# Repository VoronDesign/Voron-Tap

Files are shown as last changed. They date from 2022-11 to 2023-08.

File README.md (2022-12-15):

# Voron Tap

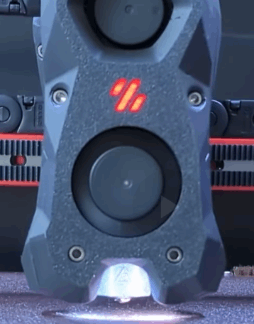
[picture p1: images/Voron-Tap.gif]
Voron-Tap3


> Animated image courtesy of [Maple Leaf Makers](https://github.com/MapleLeafMakers) , see the whole video at https://www.youtube.com/watch?v=mz5qcOZgXhI

Tap is a nozzle-based z-probe for the V2 and Trident printer designs. The entire toolhead moves to trigger an optical switch. Tap offers many advantages:

* Extreme precision 0.4μm (0.0004mm)
* Any build surface and easily change at will
* Durability via optical sensor (millions of probe cycles)
* High temperature reliability (70C to 100C)
* Simplified probe mechanics (no dock/undock macros)
* No separate Z-endstop required
* Crash protection

## Requirements

* Bed must be stable for probing force of 500-800 grams
  * Switchwire, V1.8, Legacy, V0 beds are NOT rigid enough
* Mounts to MGN-12H X-axis
* Front mounted extruder (Clockwork2, LGX, Galileo)
* Accuracy depends on good mechanical condition
* Must have 5V at toolhead or special 24V sensor PCB

## Instructions

Comprehensive assembly details are available in the [Manual](Manual/Assembly_Manual_Tap.pdf)

## Post-Install Setup

1. Update your `printer.cfg` as recommended in [Tap Klipper Instructions](config/tap_klipper_instructions.md)
2. Home Z and test virtual Z endstop by lifting tool-head
3. Heat soak your machine and run a couple `probe_accuracy samples=100` to "break-in" your probe
4. Run a few more `probe_accuracy` checks (default of 10 probes)

For well-built machines you can expect to see between 0.0000 and 0.0008 standard deviation.

## FAQs

* Will Tap hurt my print surface? No, probing temp is restricted to 150C. The team recommends spray coated spring steel. Users of smooth PEI may find minor burnish marks if continously probing the same spot.
* Will the hartk 2-piece PCB work with Tap? Yes, but it requires a slight modification. See discord pin.
* Can I use an optical sensor not specified in the BOM? Not recommended, the team spent considerable time validating sensors in [BOM](BOM.md).
* Can I use micro-switch instead? Not recommended, but check here for more details: [Unklicky Tap](https://github.com/majarspeed/Unklicky/tree/main/Unklicky_TAP)
* Can I use Tap with kinematic bed mounts? Yes, if your bed is rigid up to 800 grams of force.
* Doesn't this add a lot of weight? The team explored many designs and landed on ~50 extra grams as good trade-off between rigidity and weight.
* Why do I need this if my induction probe works fine? Tap enables a far better user experience as it eliminates most baby-stepping needed due to thermal expansion, nozzle & bed surface changes.
* Is Tap noticably more accurate than klicky? Yes.

## (Bonus Points) Data Science

Tap engineering is backed by data science. If you want to dive deeper check out the following resources:

* [Voron:LIVE! Voron Tap announcement stream](https://www.youtube.com/watch?v=JLUDLJQXZeU)
* [Probe accuracy across thermal envelope](https://github.com/KiloQubit/probe_accuracy)
* [Repeatability at individual corners](https://github.com/sporkus/probe_accuracy_tests)

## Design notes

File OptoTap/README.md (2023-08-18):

# OptoTap PCB

OptoTap PCB is a small, completely unnecessary PCB that exists to make installation of the optical sensor marginally more convenient. (That's right, several of us have spent dozens of hours and hundreds of dollars in order to avoid two solder joints and a bit of heat shrink.)

It comes in two official flavors/form factors:

- **V1**: smaller form factor, 5V only
- **V2**: taller form factor, 5 or 24V capable

Both simplify optical sensor installation by including the necessary current-limiting resistor for the IR led within the sensor itself, as well as providing a visible LED indicator to assist with troubleshooting. 

The V1 board attempts to minimize size and cost as much as possible, at the expense of some flexibility: it **can not be used as a drop-in replacement for 24V inductive sensors** (24V will fry the optical sensor, eventually.)

The V2 board adds a switch-mode regulator to allow safely connecting to 24V probe headers. The regulator converts positive input voltage between >5V and 24V to 5V on-board, at the expense of some additional components and a larger PCB. **Please read important information about previous versions of this board below.**

## OptoTap V1

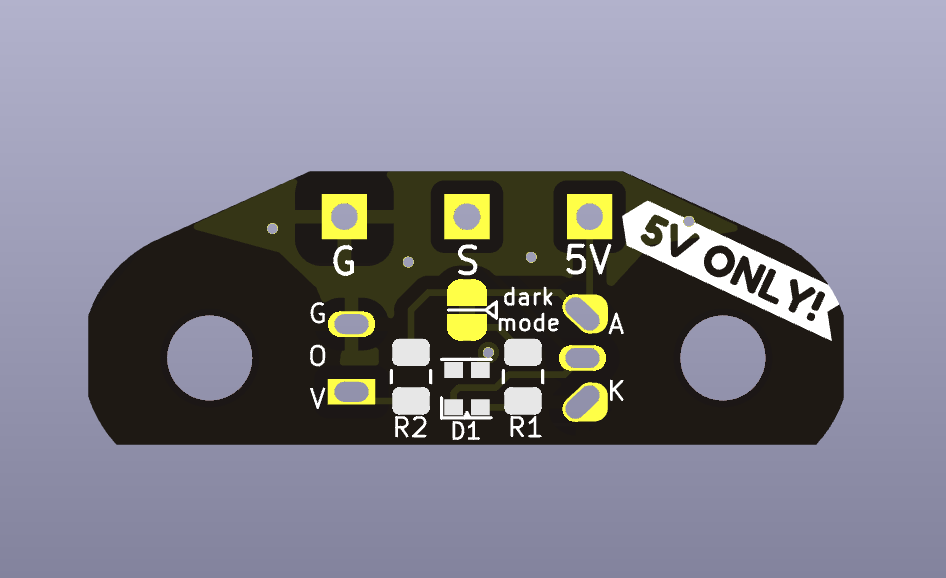
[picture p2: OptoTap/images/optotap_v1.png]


This version saves some vertical room by requiring you to solder your connector wires directly to the board.

**Do not connect this version to 24V!** (Did we mention that *it's not 24V tolerant???*) Many of the Voron toolhead PCBs in circulation send 24V to the three-pin probe header. You cannot plug this board directly in to these headers!

### Revision history 

- 1.0: initial release
- 1.3: updated release
	- hybrid footprint to permit use of EE-SX398 sensor in addition to Optek versions
	- two-color LED to indicate status and assist with troubleshooting.
	- 'Dark Mode' solder jumper to allow turning off indicator LEDs
	- increased thermal relief on solder pads to make through-holes easier to solder

## OptoTap V2

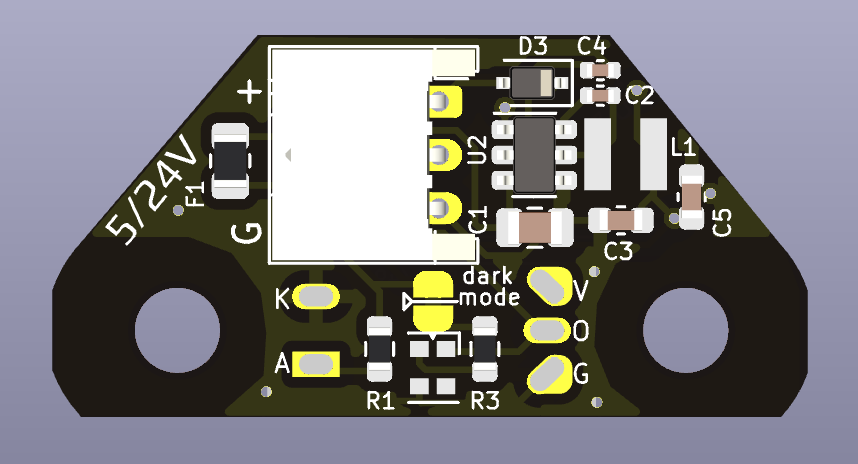
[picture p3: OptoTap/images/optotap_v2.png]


This version uses an AP63205WU switch mode regulator to drop input voltage and supply 5V to the sensor. This gives a bit of additional room to add a 3-pin JST-PH 2.0mm pitch connector as well [part number S3B-PH-K-S (LF)(SN)].

**IMPORTANT NOTE: The original version of this board had an issue that rendered it unsafe for use at 24V**. Please see [this issue](https://github.com/VoronDesign/Voron-Tap/issues/42#issuecomment-1370065351) for more extensive details on the testing and resolution of the problem. 

The current version (V2.4) fixes the inrush overvoltage spike that plagued the initial release, and adds several additional safeguards, including a polyfuse and a reverse polarity protection diode.

### Usage notes

#### Operation at 5V

The V2.4 OptoTap PCB has been tested to work fine from 5V to 24V inputs with no modifications. However, this does induce a bit of additional voltage drop from the switching regulator IC going into LDO mode. If you would like to run the V2.4 OptoTap at 5V, my first suggestion would be to just run it at 5V with no modifications. It will most likely work just fine. 

However, it does have the capacity to bypass the whole buck converter circuit. Note that this also bypasses the polyfuse, so there will be no overcurrent protection. 

To make this modification, you need to cut the trace between the center pad and 24V pad on the rear of the PCB, then use some solder to bridge the center pad to the 5V pad. To reverse the change, just desolder that bridge and re-connect the center pad to the 24V pad with more solder. 

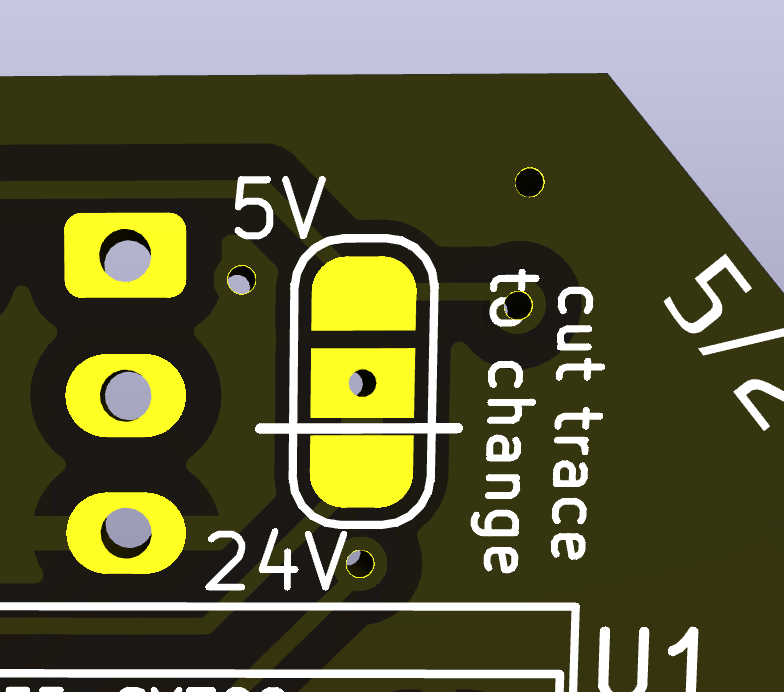
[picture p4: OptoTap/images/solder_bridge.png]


### Revision history

- 2.0: initial prototype
- 2.1: component modifications after initial testing
  - changed C1 to higher voltage rating
  - changed C2 bootstrap cap to higher capacitance
  - changed all capacitors to 0805 for better part availability
- 2.4: updated release
  - added polyfuse to limit overcurrent and damp inrush current-induced voltage spike on hot-plugging
  - added reverse polarity protection diode 
  - increased size of inductor to prevent coil saturation
  - added a second output filter capacitor to reduce output voltage ripple
  - hybrid footprint to permit use of EE-SX398 sensor in addition to Optek versions
  - two-color LED to indicate status and assist with troubleshooting.
  - 'Dark Mode' solder jumper to allow turning off indicator LEDs
  - added 5V/24V selection solder jumper on rear of board to allow for easy bypassing of voltage regulator circuit
  - increased thermal relief on solder pads to make through-holes easier to solder

### Ordering and Assembly notes

#### Inductor choice

I've tested version of this PCB with inductors from Cenker 
CKCS3012-4.7uH/M (C354557) and Microgate 
MPIT3015-4R7M-LF (C486485). Any 30xx footprint coil inductor with >1A current rating and ~ 100 mΩ DCR should work ok.

#### Indicator LED placement

For some reason, JLCPCB has trouble with their part orientation for this LED specifically. I'm hoping that eventually they will sort their database out. In the meantime, it is worth verifying the part placement prior to assembly.

The footprint silkscreen has two elements to help indicate the orientation of the LED: an extra line on the side to indicate Pin 1, and a little arrow that matches up with a corresponding arrow on the part:

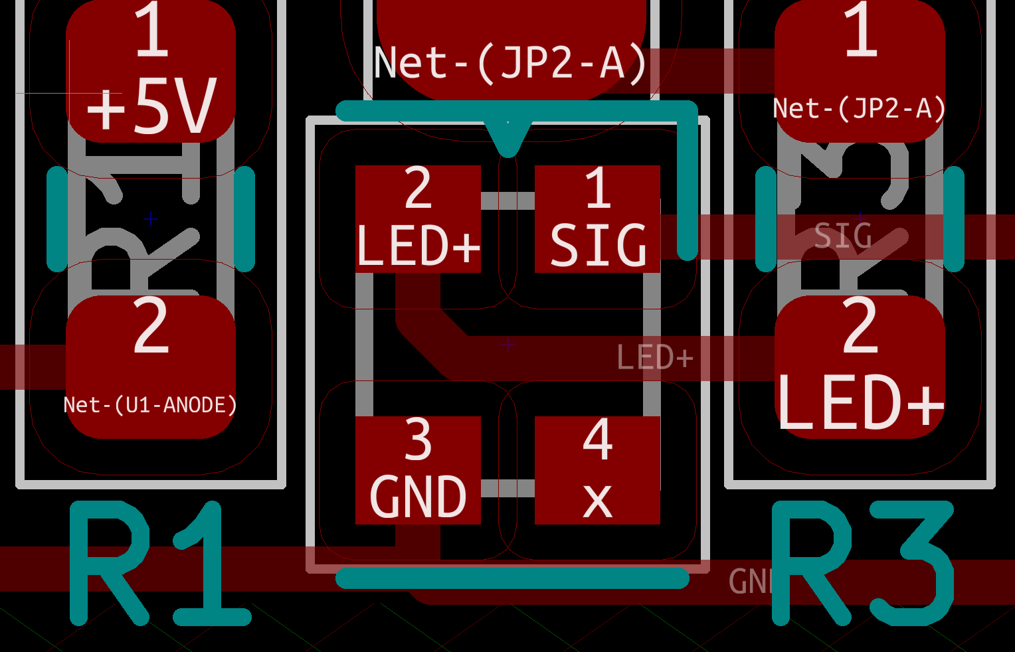
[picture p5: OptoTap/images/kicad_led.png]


For the v2.4 PCB, make sure that the arrow on the DFM points to the arrow on the footprint, pin 1 matches the extra line on the footprint, and the + pad matches up to the correct pad! 

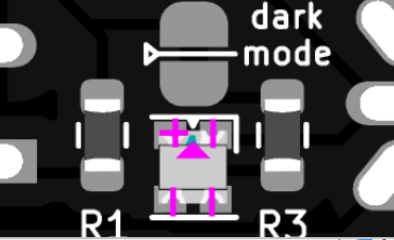
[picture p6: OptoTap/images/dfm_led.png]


This is how it will look when assembled:

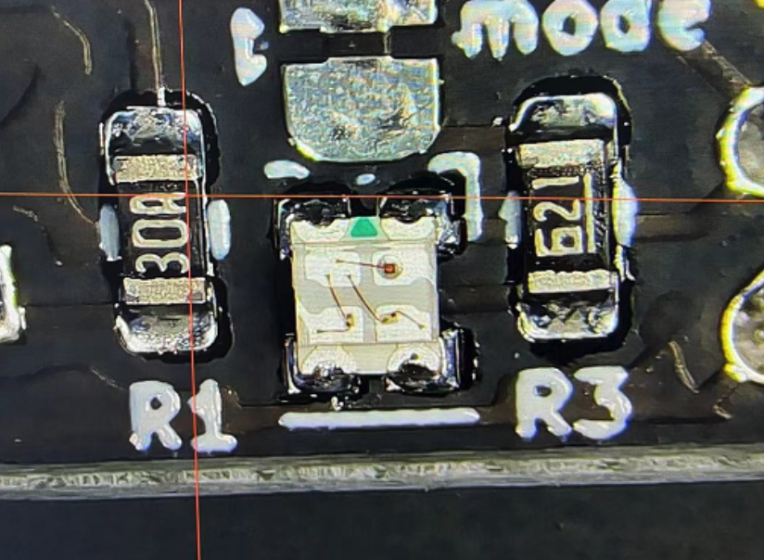
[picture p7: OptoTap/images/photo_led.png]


You can see the little bond wires from each of the three LEDs going back to the common anode, which is pretty neat.

***NOTE THAT THE 5V ONLY BOARD (V1.3) HAS A ROTATED FOOTPRINT! YOU'RE WELCOME AND I'M SORRY.***

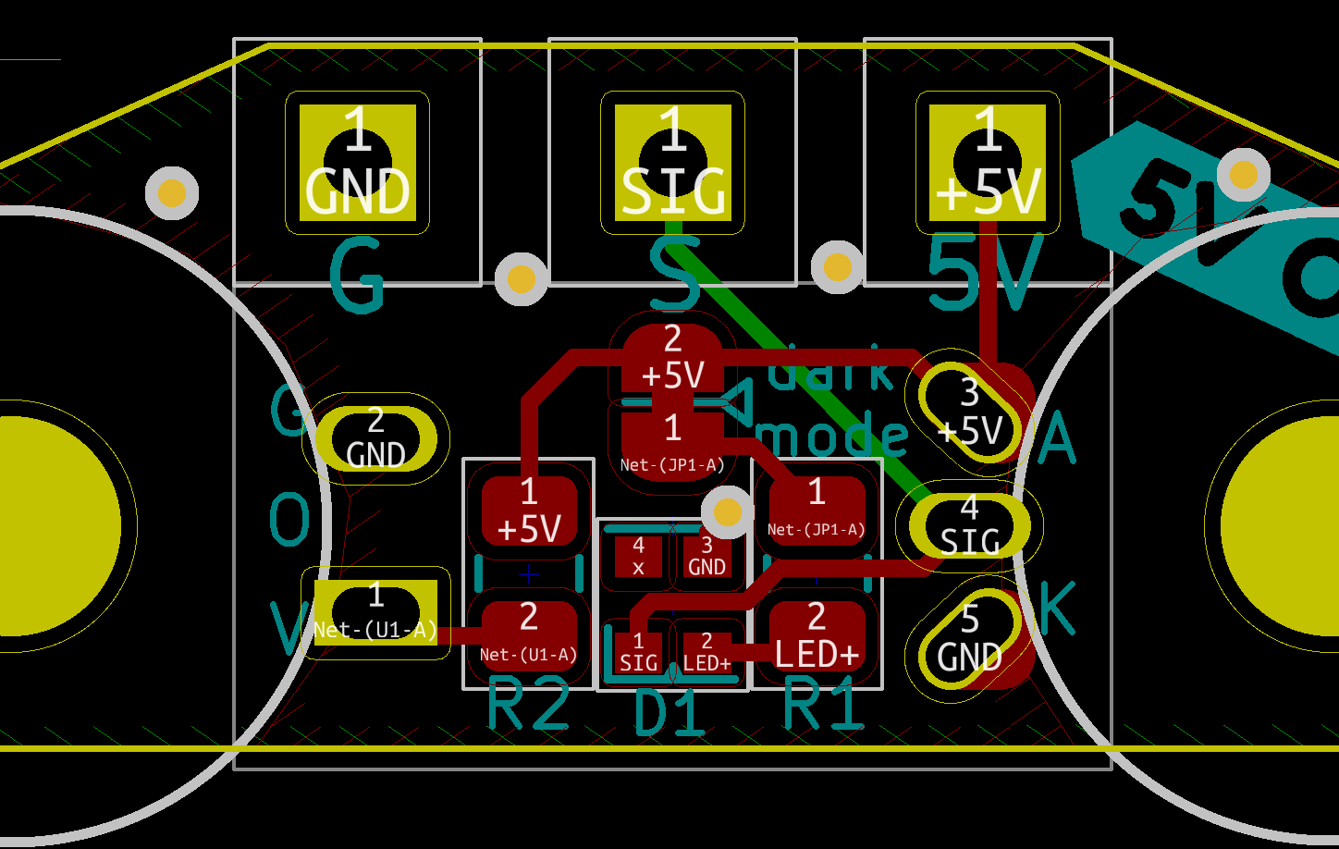
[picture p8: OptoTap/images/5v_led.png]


## Indicator LEDs

The revised boards (V1.3/2.4) now have two-color indicator LEDs to help assist with troubleshooting. This should hopefully help a little bit with troubleshooting. The expected behavior of the LED is:

- Blue: Connected to power, beam not broken
- Red: Connected to power, beam broken

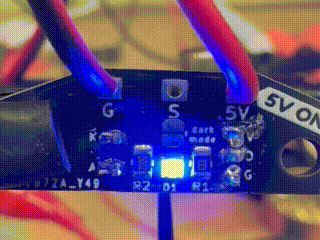
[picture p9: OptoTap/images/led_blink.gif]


When installed in the toolhead, the light should be red normally (toolhead in 'down' position) and blue when activated (toolhead in 'up') position.

I would suggest powering on the board with 5V prior to installing it to make sure everything is functioning as expected. If the indicator LED is red with nothing blocking the optical sensor beam path, there is probably a problem with the ground and signal wires -- triple check!

## Sensor Choice

### Omron or Optek

The revised versions of the boards (V1.3 and V2.4) feature a hybrid optical sensor footprint that permits installation of the Omron EE-SX398 sensor in addition to the Optek OPB666/9xx versions. In testing, the Omron sensor performed just as well as the Optek sensor. 

However, it has a *slightly* different footprint than the Omron sensor, with annoyingly-close leads on the three pin side. I went through a few iterations of testing to come up with a hybrid footprint that seems to work well for either sensor model.

The slots mean there is a little play in sensor positioning, particularly with the EE-SX398 sensor. To help ensure precise alignment with this sensor, print out the jig included in the [STLs](./STLs) folder.

### Sensor Logic

The Tap setup requires a *buffer* style circuit rather than an *inverter* style to ensure safe operation. This style causes the sensor to trigger (pull the signal pin low) when the toolhead is in its normal, 'down' position. That means that if there is a bad connection somewhere, the MCU can observe that there is a problem *without* crashing the toolhead uncontrollably into the build plate.

Please double check your sensor part number to make sure you're getting the appropriate model!

#### For Omron:

- **Good**:
  - EE-SX398
- **Bad**: 
  - EE-SX498

#### For Optek:

- **Good**: 
  - OPB666N
  - OPB9x1
- **Bad**:
  - OPB9x2

Additionally, for the Optek probes, the OPB9x0 sensors are totem pole rather than open collector, meaning that they will pull the sense pin up to 5V when not pulling it down to GND. This can cause problems for some boards (notably RP2040-based CAN toolhead boards) that do not have 5V-tolerant endstop pins.

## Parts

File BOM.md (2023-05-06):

# Bill of Materials

|Category|Qty|Description|Notes|
|:----|:----|:----|:----|
|Hardware|1|50 mm MGN9 Rail|see cutting guide, Ends deburred, overall length +/- 1 mm|
|Hardware|1|MGN-9H Carriage|Medium preload (Z1) is preferred, but regular preload will work. Carriage must be removable from rail.|
|Hardware|2|6 mm x 3 mm magnet|6 mm diameter, 3 mm tall cylinders.  N52 strength preferred,  N35 or higher strength required.|
|Hardware|11|M3 Heatset Insert|Standard Voron spec 4.7 mm diameter inserts|
|Hardware|3|H3 Hex Nut|ISO 4032|
|Hardware|8|M3 Washer|DIN 125, 7mm outer diameter, 0.5 mm thickness|
|Hardware|2|M3 x 20 SHCS|Socket head cap screw|
|Hardware|3|M3 x 16 SHCS|Socket head cap screw|
|Hardware|3|M3 x 12 SHCS|Socket head cap screw|
|Hardware|1|M3 x 6 SHCS|Socket head cap screw|
|Hardware|2|M3 x 6 FHCS|Flat head cap screw. MUST BE MAGNETIC.  No stainless, may be black oxide or zinc coated.|
|Hardware|2|M3 x 12 BHCS|Button Head Cap Screw|
|Hardware|2|M3 x 8 BHCS|Button Head Cap Screw|
|Hardware|10|M3 x 6 BHCS|Button Head Cap Screw|
|Hardware|2|M3 x 50 BHCS/SHCS|Button or Socket Head Cap Screw, fully threaded|

Optionally you can replace the M3 x 6 FHCS with additional magnets. See [R8_errata.md](Manual/R8_errata.md) for details

## Sensor Options:  Select either “Wired Sensor” or “PCB Sensor"

**Wired**
|Category|Qty|Description|Notes|Links|
|:----|:----|:----|:----|:----|
|Electronics|1|220 Ohm resistor | ¼ Watt, +/- 10% tolerance resistor| |
|Electronics|1|OPB Wired Sensor|Optek sensor, wired. OPB991| |
| | | |OPB991P51Z| |
| | | |OPB991L51Z| |
| | | |OPB991T51Z| |
| | | |OPB991T11Z|https://www.digikey.com/short/rrjtmvwm|
| | | |OPB991L11Z|https://www.digikey.com/short/cnnhjr5n|

**PCB Sensor**
|Category|Qty|Description|Notes|Links|
|:----|:----|:----|:----|:----|
|Electronics|1|OptoTap v2 PCB| | |
|Electronics|1|OPB PCB Sensor|Optek sensor: OPB666N or OPB971N51| |
| | | |OPB666N|https://www.digikey.com/short/f2mzw5rm|
| | | |OPB971N51|https://www.digikey.com/short/m9rz73fp|

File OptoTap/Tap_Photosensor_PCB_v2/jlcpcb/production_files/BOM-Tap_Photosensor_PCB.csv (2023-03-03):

Comment | Designator | Footprint | LCSC
D_Schottky | D3 | D_SOD-323 | C146335
AP63205WU | U2 | TSOT-26 | C2071056
620R | R3 | R_0603_1608Metric | C23220
Polyfuse_Small | F1 | R_0805_2012Metric | C2840557
100 nF | C2 | C_0402_1005Metric | C307331
4.7 uH | L1 | CKCS3010 | C354557
68 nF | C4 | C_0402_1005Metric | C354977
10 µF | C1 | C_0805_2012Metric | C440198
200R | R1 | R_0603_1608Metric | C8218
22 µF | C3,C5 | C_0603_1608Metric | C84419
XL-1615RGBC | D1 | LED_0606_1432 | C965840

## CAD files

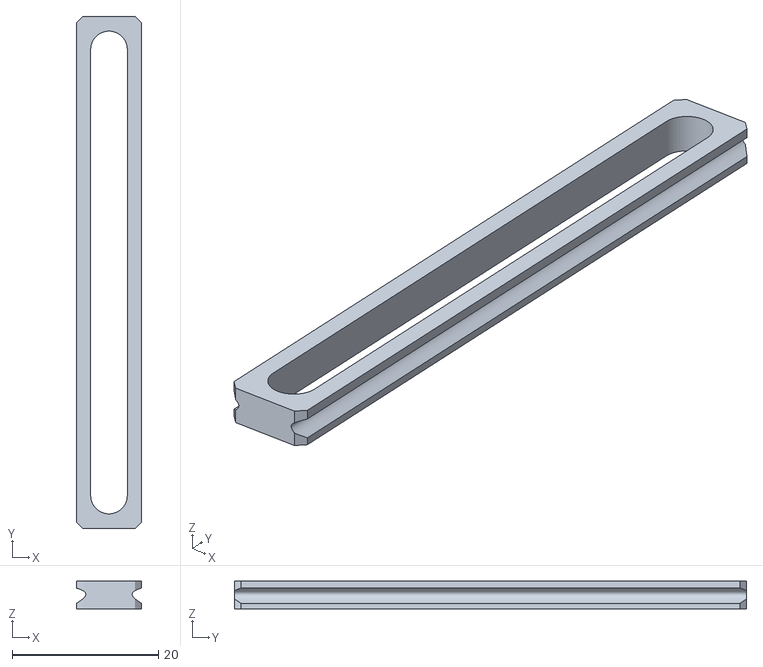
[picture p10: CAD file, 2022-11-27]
STLs/MGN9_Assembly_Tool.stl
8.90 x 70.0 x 3.80

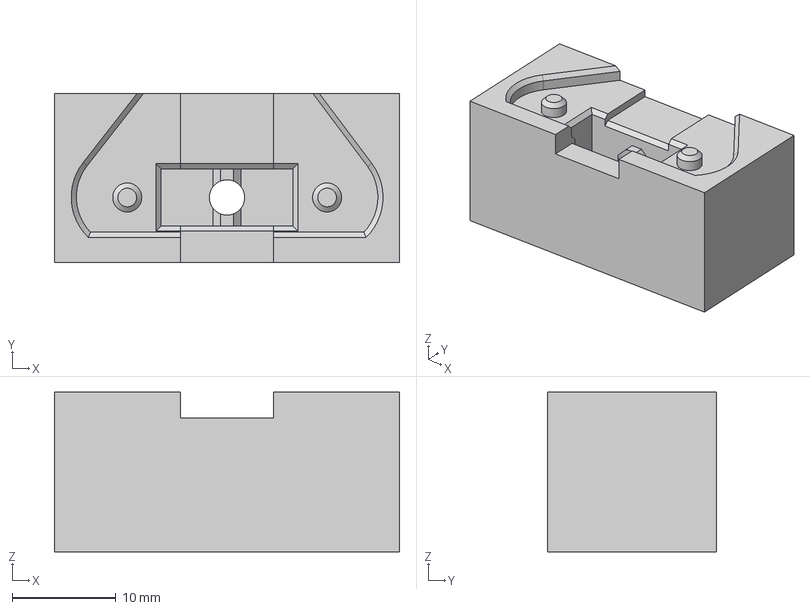
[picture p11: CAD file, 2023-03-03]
OptoTap/STLs/solder_jig.step
33.2 x 16.2 x 15.4 mm

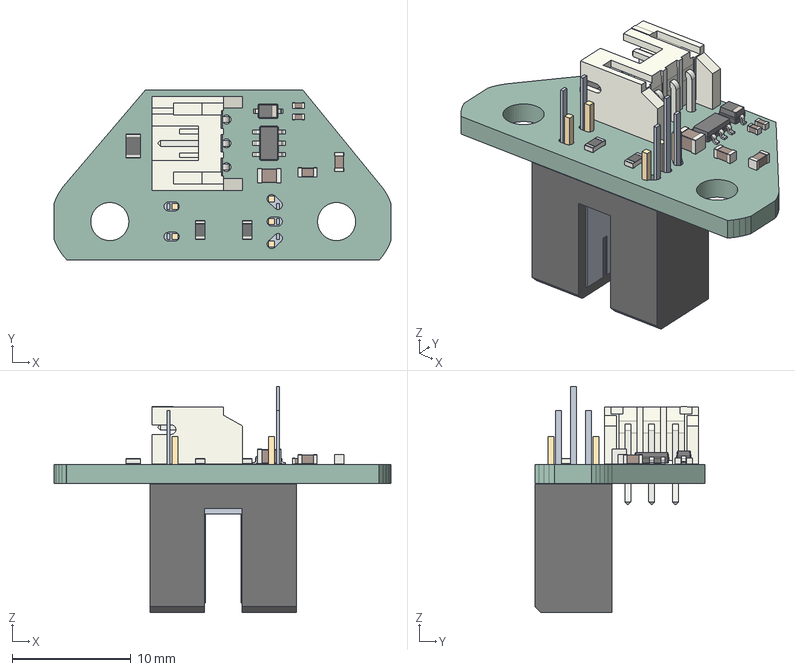
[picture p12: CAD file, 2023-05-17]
OptoTap/Tap_Photosensor_PCB_v2/Tap_Photosensor_PCB.STEP
28.3 x 14.3 x 19.0 mm
PCB

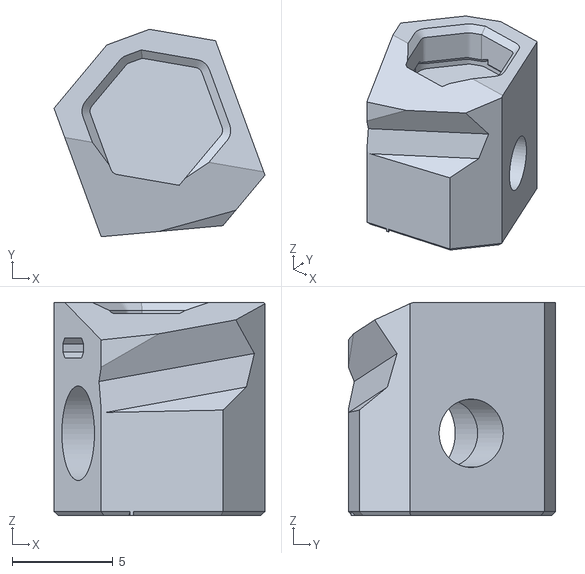
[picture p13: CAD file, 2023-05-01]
STLs/Tap_Center_right_r8.stl
10.5 x 10.3 x 10.6

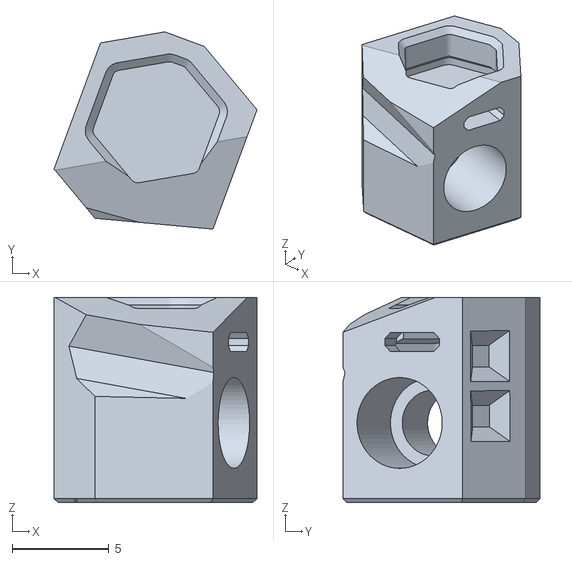
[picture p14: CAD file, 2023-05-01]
STLs/Tap_Center_left_r8.stl
10.5 x 10.2 x 10.6

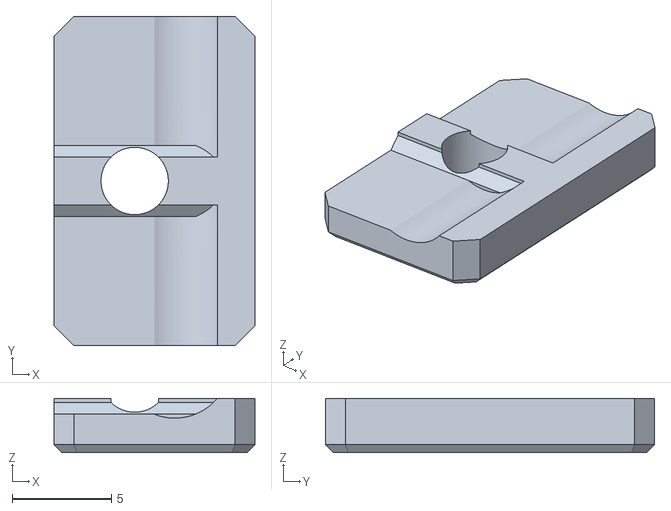
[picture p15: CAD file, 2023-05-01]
STLs/[a]_Tap_Belt_Cover_r8_x2.stl
10.1 x 16.6 x 2.74

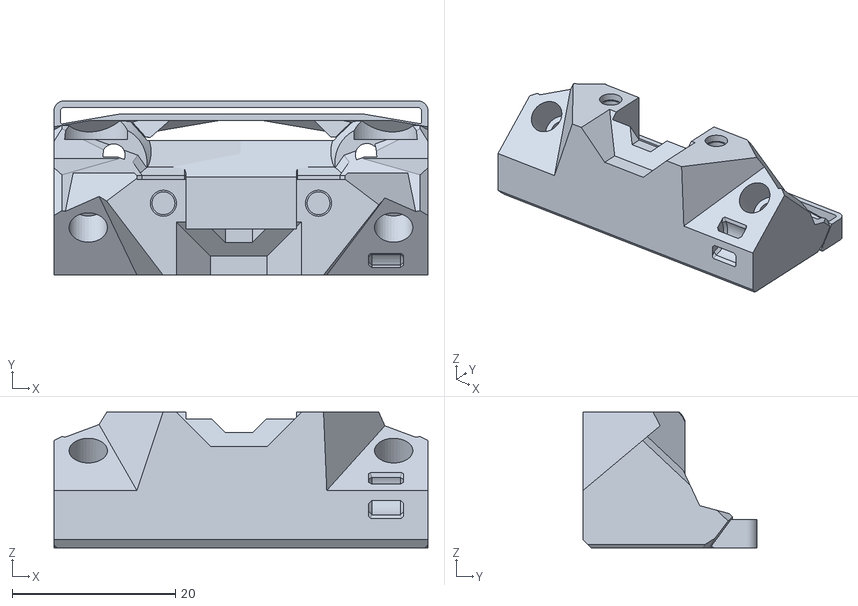
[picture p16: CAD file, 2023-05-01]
STLs/Tap_Upper_PCB_r8.stl
45.8 x 21.3 x 16.6

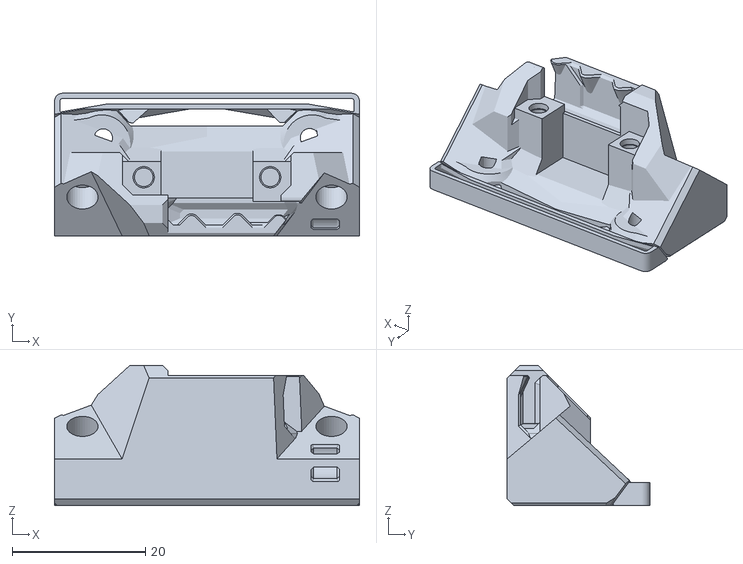
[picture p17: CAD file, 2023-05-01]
STLs/Tap_Upper_Wired_r8.stl
45.8 x 21.4 x 21.1

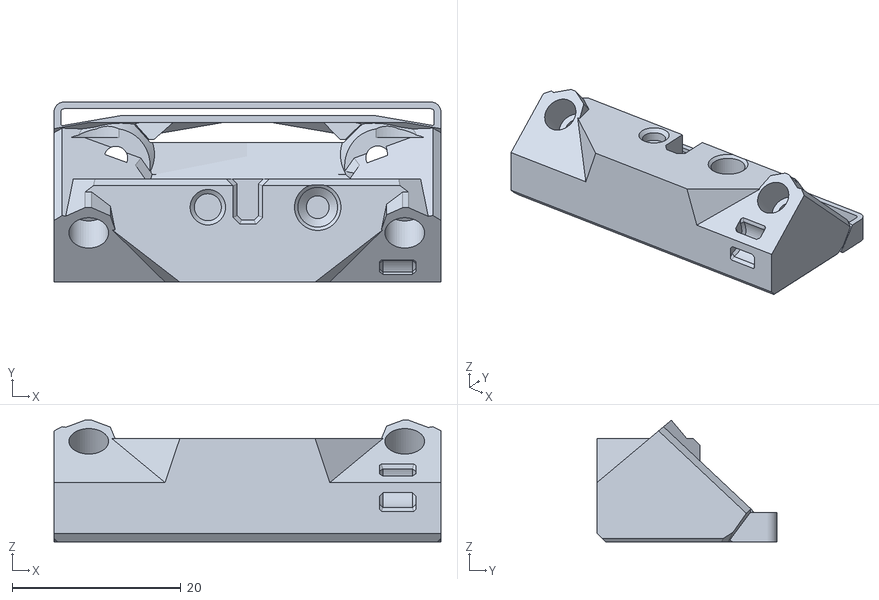
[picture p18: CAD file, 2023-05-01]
STLs/Tap_Upper_D2HW_r8.stl
45.8 x 21.3 x 14.4

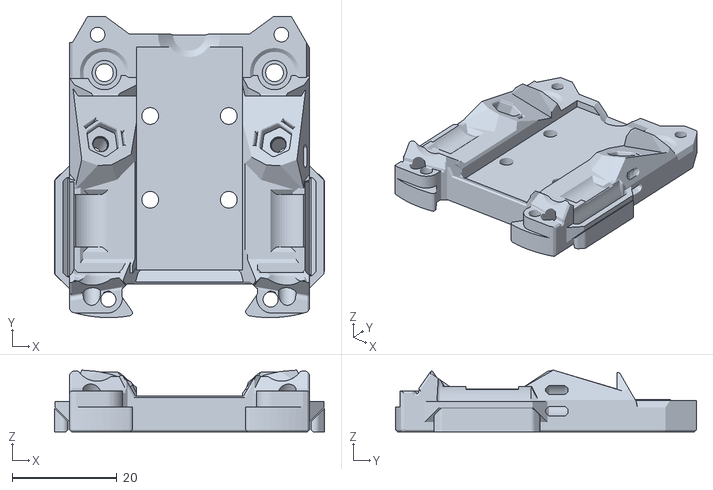
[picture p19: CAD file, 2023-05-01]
STLs/Tap_Front_r8.stl
51.6 x 57.5 x 11.8

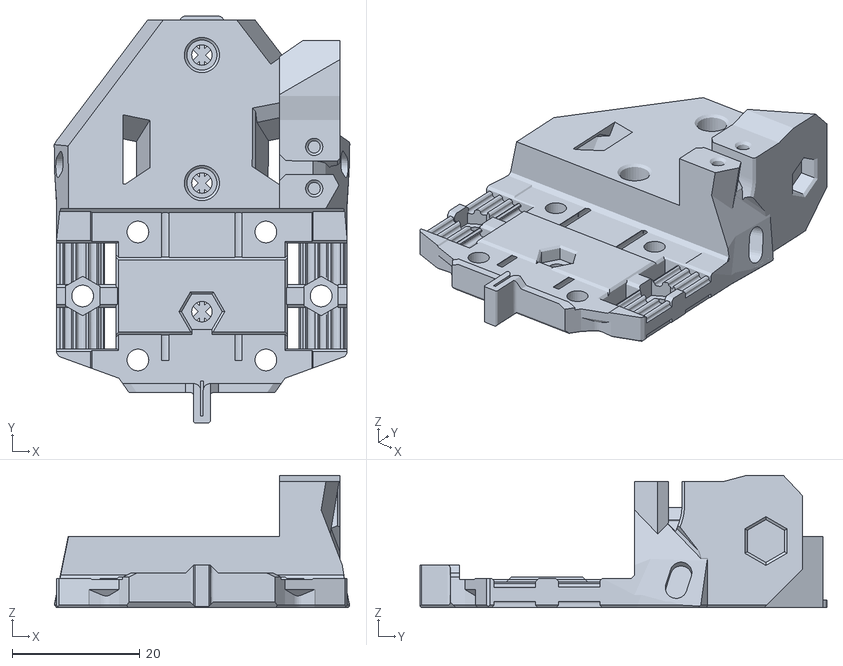
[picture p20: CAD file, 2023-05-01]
STLs/[a]_Tap_Center_r8.stl
46.2 x 63.6 x 20.7

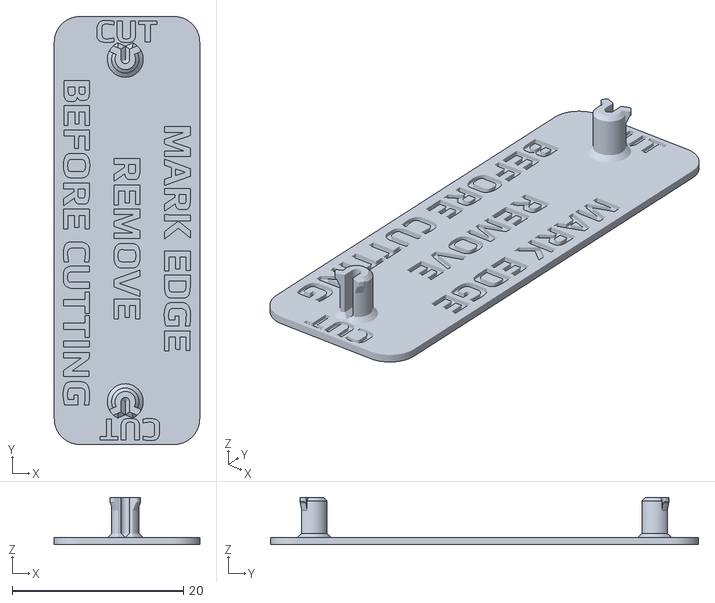
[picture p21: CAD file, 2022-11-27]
STLs/Printed_Cut_Guide.stl
17.0 x 50.0 x 5.50

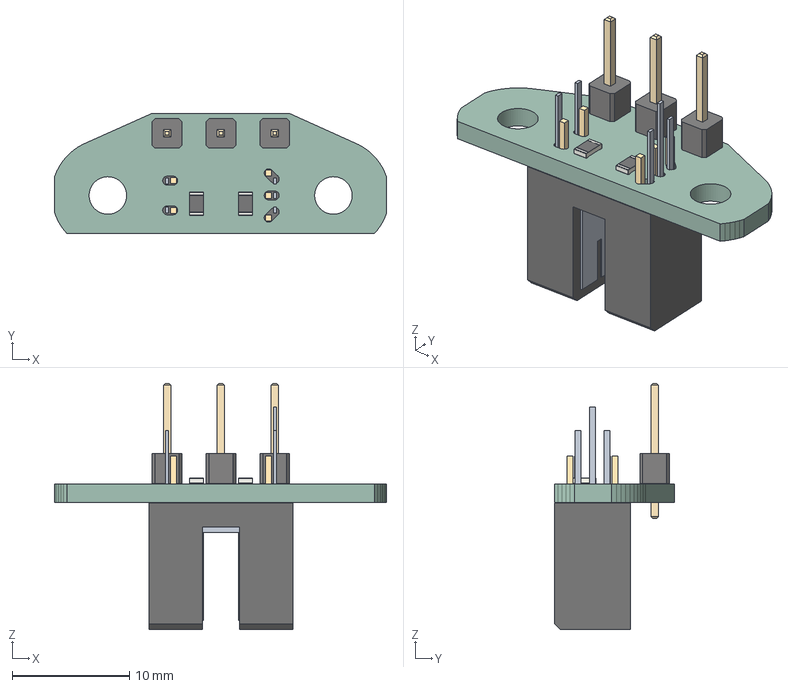
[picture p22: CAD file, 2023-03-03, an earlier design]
OptoTap/Tap_Photosensor_PCB_v1/Tap_Photosensor_PCB_Short_ee-sx.STEP
28.3 x 10.2 x 21.0 mm
PCB

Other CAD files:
OptoTap/STLs/optotap_eeSX398_solder_jig.stl
OptoTap/Tap_Photosensor_PCB_v2/Tap_Photosensor_PCB_v2.4.STEP

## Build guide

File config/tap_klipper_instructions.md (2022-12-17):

# Updating your Klipper config for Tap

There are a few changes you'll need to make in order to get Tap working properly.

1. Update your Z endstop: 
   
   - Under the `[stepper_z]` block, you'll want to comment out your `position_endstop` and change your `endstop_pin` so that it uses the virtual Z endstop for Tap.
   
      - Example: `endstop_pin: probe:z_virtual_endstop`
   
   - Be sure to *also* remove any automatically saved `[stepper_z] position_endstop: ...` value that may be found at the **bottom** of your `printer.cfg`file.

2. Update your Z homing position: 
   
   - If you use `[safe_z_home]`, change the location to the center of the bed. If you have a `[homing_override]` make sure that it moves the toolhead to the center of the bed before calling `G28 Z`.
   
3. Update your probe's offsets: 
   
   - Remember, with Tap, your nozzle IS the probe, so your `[probe] x_offset` and `[probe] y_offset` values should be 0 now. You'll need to manually calibrate the probe's Z offset by using `PROBE_CALIBRATE`.
   
4. Add Tap's `activate_gcode:`  
   
   - This G-code will allow you to probe cold, but will also prevent you from probing with a nozzle at printing temperature (to try to preserve your build surface). This goes in the `[probe]` section of your config.  

```jinja

activate_gcode:
    {% set PROBE_TEMP = 150 %}
    {% set MAX_TEMP = PROBE_TEMP + 5 %}
    {% set ACTUAL_TEMP = printer.extruder.temperature %}
    {% set TARGET_TEMP = printer.extruder.target %}

    {% if TARGET_TEMP > PROBE_TEMP %}
        { action_respond_info('Extruder temperature target of %.1fC is too high, lowering to %.1fC' % (TARGET_TEMP, PROBE_TEMP)) }
        M109 S{ PROBE_TEMP }
    {% else %}
        # Temperature target is already low enough, but nozzle may still be too hot.
        {% if ACTUAL_TEMP > MAX_TEMP %}
            { action_respond_info('Extruder temperature %.1fC is still too high, waiting until below %.1fC' % (ACTUAL_TEMP, MAX_TEMP)) }
            TEMPERATURE_WAIT SENSOR=extruder MAXIMUM={ MAX_TEMP }
        {% endif %}
    {% endif %}
    
```

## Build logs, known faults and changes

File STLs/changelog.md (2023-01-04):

The scope of this file is to summarize any stl changes after the initial release files (r1)
Important note:  When a change is made it is normal for only a few parts to change, or a single part to change.  For parts that don't change, we do not increment revision numbers.
As a result of this, the revision numbers of the most current parts may not match.

11/28/2022
[a]Tap_Center_r2: fixed a minor issue in the MGN12H chamfer that would cause some MGN12H carriages to not fit properly (issue 15)
https://github.com/VoronDesign/Voron-Tap/issues/15

11/29/2022
[a]Tap_Center_r3: re-added in the support structure that went missing at [a]Tap_Center_r2

12/16/2022
[a]Tap_Center_r4: reinforced area above magnet holders
Tap_upper_D2HW_r1: new variant for switch
Tap_upper_PCB_r2: minor changes to optical sensor location for better trigger
Tap_upper_wired_r2: repositioned sensor to same location as PCB
Tap_front_r2: increased clearance to M3x12 endstop

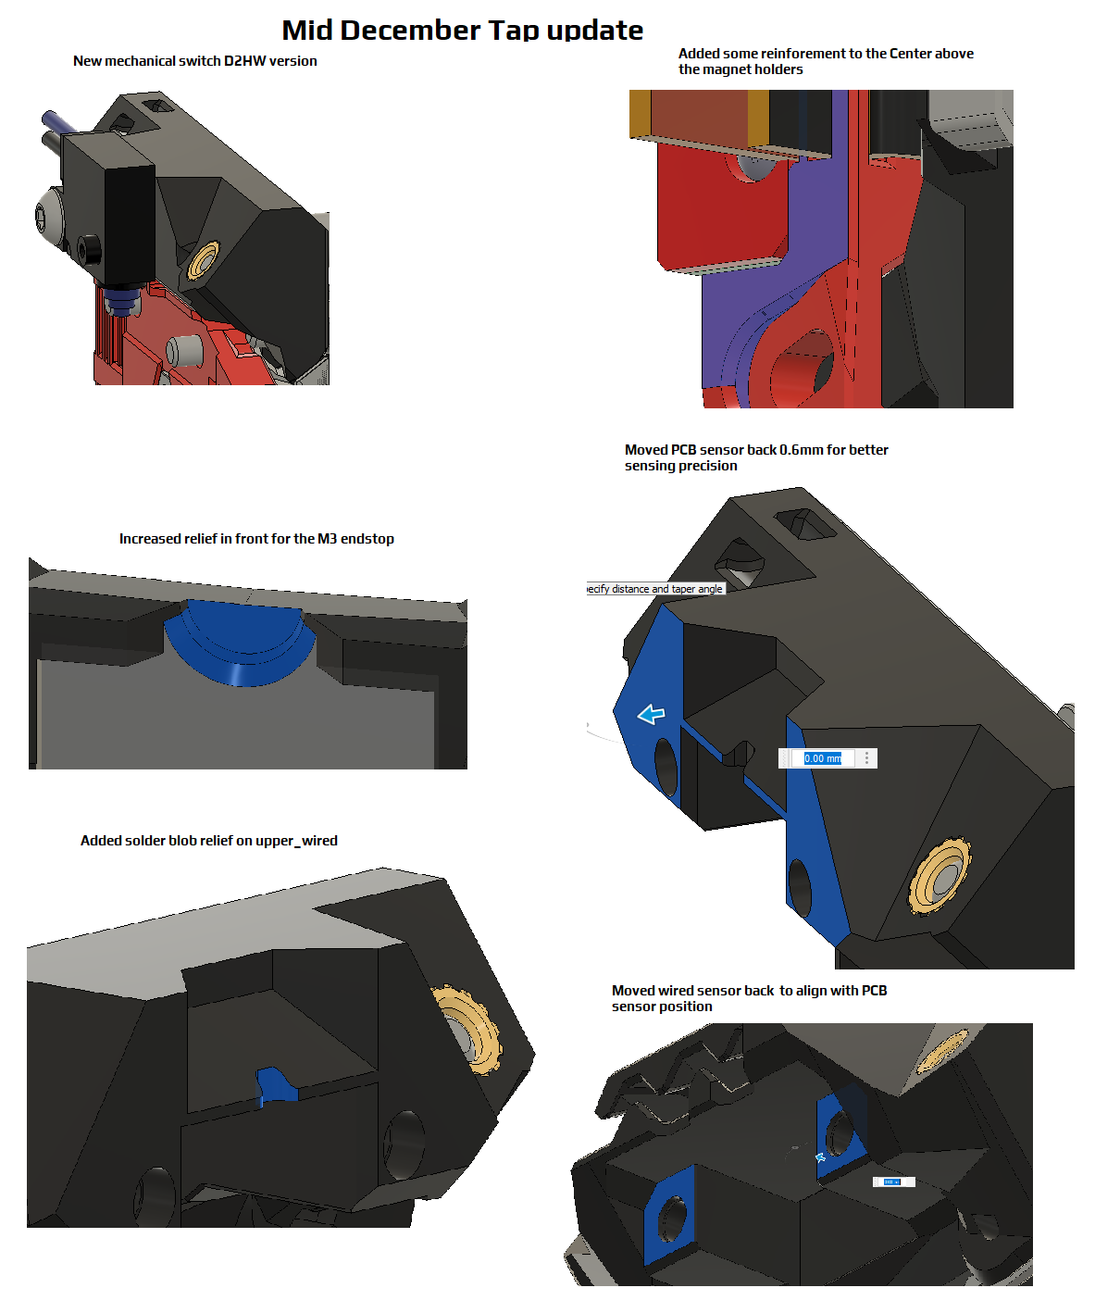
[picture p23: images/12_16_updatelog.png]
Mid December Update


1/3/2023
[a]Tap_Center_r5: eliminates binding issues caused by belts pressing on endcaps, also better belt management
moved X-switch 1mm to right to activate before collision
[a]Tap_Center_r6: removed a small artifact that began in r5
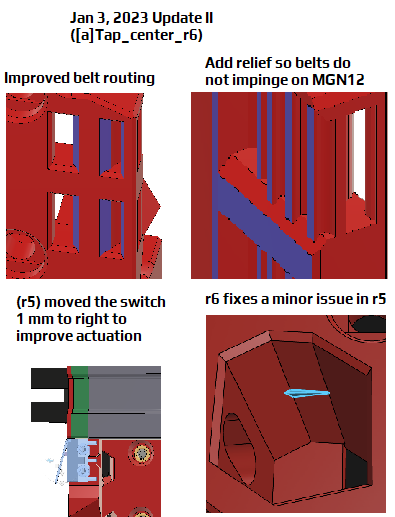
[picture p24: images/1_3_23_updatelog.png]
Jan 3 Update


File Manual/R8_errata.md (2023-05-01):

TAP RC8 Errata, notes, etc

Welcome to Tap RC8.  This is a full reprint from Tap RC6.

*Wait! What happened to RC7? the last thing you published was RC6!*  
RC7....didn't make it.  From its ashes, RC8 arose.  As we all know, eight is great.  
  
Here's what changed:

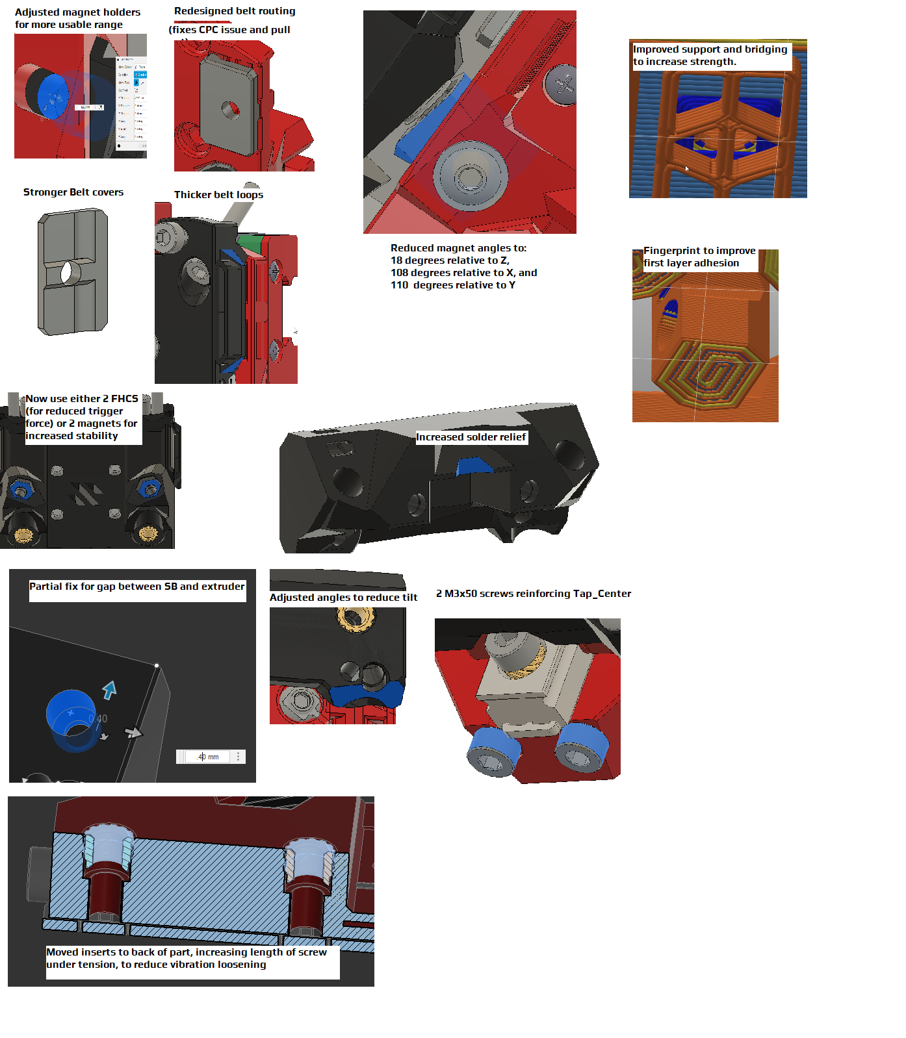
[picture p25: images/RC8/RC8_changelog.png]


One of the big changes is you can now use either a pair of magnets or a pair of FHCS in Tap_front.  The stronger the pull force, the more resistant to ringing, but also the more potential to marring your Build surface.  
  
here are my reccommendations.  this is a guideline only, your mileage may vary, caveat emptor, barba crescit caput nescit.

| Build surface | Trigger force (approx) | Configuration | Max Accels |
|---|---|---|---|
| Flat PEI sticker | 750 g | 2 N35 magnets + 2 FHCS | 5000 mm/s^2 |
| Powder coat PEI | 1400g | 4 N52 Magnets | 10000 mm/s^2 |

Other than possibly wanting more or stronger magnets, here's what you will need in addition to the original Tap BOM:

| Qty | Description | Notes |
|-----|---|---|
| 2 | M3x50 BHCS or SHCS | Threaded the entire length. you can get by without these, or with M3x40's.  |
| 1 | M3x16 SHCS | Replaces a M3x12 SHCS securing the rail. |
| 2 | M3x8 BHCS | Used with belt covers |
| 2 | M3 nuts | Used with belt covers |
| 2  | M3 washers | Used with belt covers |
| 11-12 | M3 Heatset inserts | This depends on your ability to reclaim heatsets from the existing parts.  If you can, you won't need any additional heatsets. |

Belt handling:  
The belts are now handled by looping around Tap_center, and secured with a printed belt cover and M3x8 BHCS:

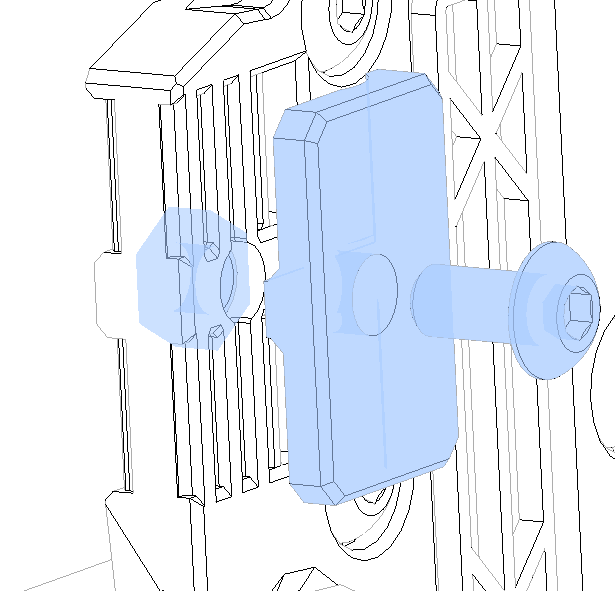
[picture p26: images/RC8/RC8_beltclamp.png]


the 2 M3x50 bolts are threaded up into Tap_Center, and serve to provide extra stiffening:

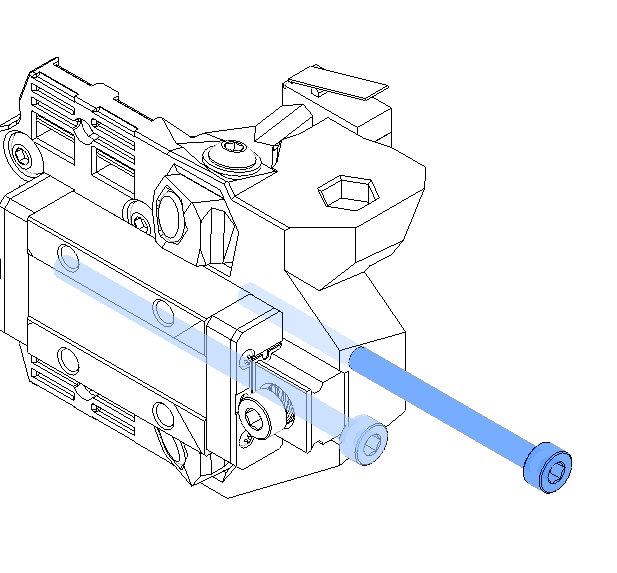
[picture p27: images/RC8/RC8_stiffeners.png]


The heatset inserts for the center are moved back 4 mm to provide extra vibration resistance:

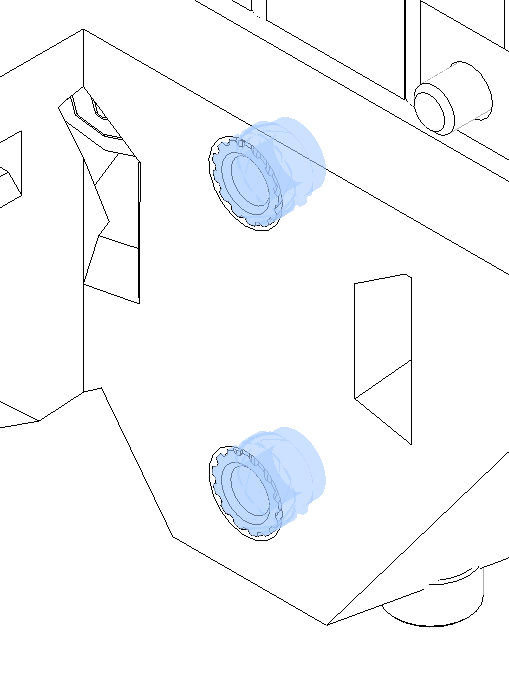
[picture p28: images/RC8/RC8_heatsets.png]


So they will need to be secured with M3x12 and M3x16 SHCS:

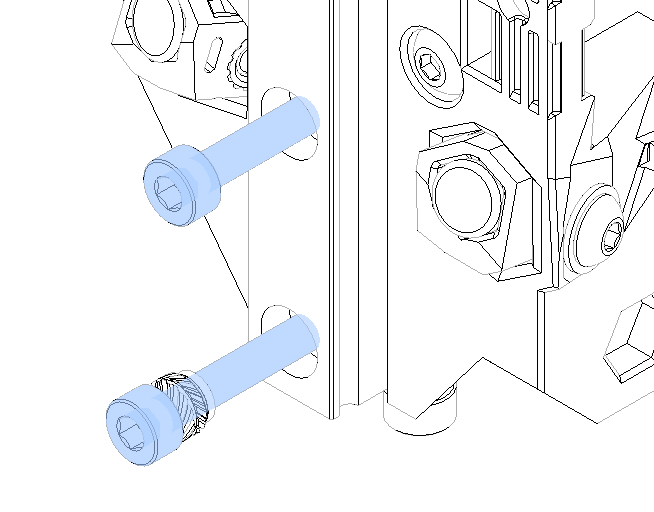
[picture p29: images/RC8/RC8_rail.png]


(The top is still secured by M3x6 SHCS)

Enjoy!

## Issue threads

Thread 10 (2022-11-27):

Fun Fact Voids™

Durahl, 2022-11-27:
The on Page 27 of the Manual mentioned `Fun Fact Voids™` didn't appear with my settings of **SuperSlicer** and since I couldn't figure out what settings was responsible for them not to make an appearance I went ahead and enlarged them to a 0.2mm gap which then sliced them as intended.

Maybe consider increasing them in the STLs like I did or give a mention in the Manual what Slicer setting may be responsible for them to appear ( or not )?

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

pl4nkt0n, 2022-11-28:
You can see them within the STEP:
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

I think, your slicer is closing this gaps because of too high "gap closing radius". There should be the same function with different names in different slicers.

notgwj, 2022-11-28:
The SuperSlicer setting that causes this is actually `hole_size_compensation` (`XY compensation`).  Setting it to zero makes the voids work as intended.  See https://discord.com/channels/460117602945990666/1041007230239125574/1046753665270165574

Badnoob-327, 2022-12-13:
"This part has thin voids inside it (blue).  When the part is sliced, these produce internal ribs which strengthen the part.  If your slicer closes these up, recheck your slicer settings for hole size compensation. Default voron slicer profiles are available for voron printers."

Hows that? I wanted to keep it general as there are other settings that could affect this.

notgwj, 2022-12-13:
Looks good to me.

nemgrea, 2022-12-27:
fixed via https://github.com/VoronDesign/Voron-Tap/pull/32

Closed 2022-12-27.

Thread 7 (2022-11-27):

(small) Error in the Assembly Manual

laserbeak, 2022-11-27:
Hi,
Just wanted to point out a small error in the assembly manual. An unfinished sentence(or did I miss the punchline?).
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

laserbeak, 2022-11-27:
OOH! And another.
Looks like there's some truncation happening?
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

Badnoob-327, 2022-11-27:
and some pictures got pixelated out as well.

nemgrea, 2022-11-28:
will be fixed via https://github.com/VoronDesign/Voron-Tap/pull/16

Closed 2022-11-28.

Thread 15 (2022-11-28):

MGN12 Carriage does not lay flat on Tap_Center

joseph-greiner, 2022-11-28:
I was looking at the CAD for the Tap an noticed interference between the MGN12 carriage and the tap_center component. I printed the STL in the repo, mounted the carriage with the belts installed and noticed that the parts mount at a slight angle to each other.

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

The issue is that the chamfer for the bottom of the carriage on the tap_center part is too big and will not let the carriage lay flat, even with belts installed.

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

By cutting out the large chamfer and adding a 0.4mm chamfer to the area the carriage now lays flat.

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

Modified STL and STEP files can be provided if requested.

Badnoob-327, 2022-11-28:
it appears that some MGN12's have a different chamfor spec than others, I will update the STL.

Badnoob-327, 2022-11-29:
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

please look at the updated tap_center_r2 file and let me know if you see need for more than that, I like to keep some chamfer there if possible

joseph-greiner, 2022-11-29:
I am printing it now, I will update when it is finished, but the support was not exported with the part STL.

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

joseph-greiner, 2022-11-29:
Printed the r2 STL, the carriage sits flat now.

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

Badnoob-327, 2022-12-06:
I think this can be closed now, thank you for your feedback.

Closed 2022-12-06.

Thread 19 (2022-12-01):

Wrong link to "Tap-Klipper Instructions"

GuidoHendriks, 2022-12-01:
First things first; I'm so impressed with this project! Thanks a lot. 👍🏻

---

Now the minor issue with the manual...

On page 37 of the manual it says:

> The software setup and other initial setup steps with your new printer can also be found on our documentation page. We recommend starting with the **Tap-Klipper Instructions** on our Github.

This contains a wrong link.

Have double checked that I have the latest file. Also noticed this https://github.com/VoronDesign/Voron-Tap/issues/14 which also does not seem to be fixed in the latest file. Maybe it's not committed or pushed to Github yet?

Badnoob-327, 2022-12-13:
got it , and I rerefixed the #14, appreciate the reminder.

nemgrea, 2022-12-27:
fixed via https://github.com/VoronDesign/Voron-Tap/pull/32

Closed 2022-12-27.

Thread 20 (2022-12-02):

Assemble Sensor instructions should address position of solder work

ditdafivo, 2022-12-02:
I assembled my OBP991T11Z to basically look identical to the picture on the manual page 13, even to the same scale, but as a result there isn't enough space to route the wires with the shrink tube, soldering joints etc. in the wiring channel of Tap_Upper_Wired_r1.stl.

I'm thinking now the best place for all the solder work is so that it lives along side all the rest of the concealed wiring for the tool head.  In fact for the second try, I might not even do that solder work until the sensor body is screwed into Tap_Upper_Wired and the wires are installed in the wiring channel. I'm not sure if that's what others are doing or if specific length guidelines can make sense to document in the manual given the variety of toolheads, canbus mods etc.  But at least it would be helpful to note on that manual page that the picture is not meant to show the extra length required between the sensor body and the resistor/solder work/shrink tube to route through the wiring channel.

ditdafivo, 2022-12-05:
Having now fitted my stealthburner/CW2, I'd leave at least 30mm wire untouched out of the sensor body to be able to conceal with work safely under the toolhead wiring cover.

kyleisah, 2022-12-13:
@ditdafivo hey there, I made the graphic you're referring to. It wasn't really *intended* to be used to scale, but I can see how that would happen, and I think I would feel better having the actual components being tucked inside the cable door with everything else. I've got the CAD I made, wired sensors, and gumption. Maybe I just overlooked that with all the excitement. 😅 I'll talk to the right people and see what we can do to improve that.

Badnoob-327, 2022-12-16:
the intent there is actually to have the resistor tucked into the wire channel, I'll clarify the manual

ditdafivo, 2022-12-17:
I don't see how fitting inside the wire channel could have worked for my build. Maybe I needed smaller resistors/heatshrink. Or maybe I overextruded.

nemgrea, 2022-12-27:
fixed via https://github.com/VoronDesign/Voron-Tap/pull/32

Closed 2022-12-27.

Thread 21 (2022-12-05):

Holes for CW2 mounting not centered.

krankydonkey, 2022-12-05:
Upon reviewing the CAD, it appears that the holes for the CW2 Mounting on Tap Upper Wired part are off centre, causing them to be out of alignment with the CW2 holes when it is inserted into the slot.
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

Badnoob-327, 2022-12-06:
Hi, thank you for the question.  I would not use the sides as reference, as their location is determined by other geometry

I rechecked the CAD, and relative to the hotend mounting screws there is a slight offset showing of approx .08 mm. This should not cause any real issues with assembly or operation, and has not caused any issues I'm aware of.

gji, 2022-12-10:
I also noticed some more centering issues on the center body - it looks like the MGN9 rail inset is a bit less than 0.1mm off as well, from the center of the holes. Seeing as people have this working it probably doesn't matter so much functionally, but it does make any modifications a pain since the CAD is pretty far from symmetric (e.g. the belt and magnet holes are also not symmetric) so one has to be very careful when picking reference surfaces.

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

Badnoob-327, 2022-12-16:
I'm aware of it, thank you.

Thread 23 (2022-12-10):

Typo in manual about BOM heatset inserts

contrapuntal, 2022-12-10:
In the BOM on pg15: "These are standard Voron inserts, 4.7 mm diameter and 4mm tall"

4.7mm refers to the hole size in CAD. Voron standard threaded inserts are 5mm diameter.

Badnoob-327, 2022-12-13:
you are absolutely correct. thank you!

nemgrea, 2022-12-27:
fixed via https://github.com/VoronDesign/Voron-Tap/pull/32

Closed 2022-12-27.

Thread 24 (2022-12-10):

Brass threaded insert causing magnet not to sit flush

contrapuntal, 2022-12-10:
A M3x5x4 threaded insert causes bulging in the magnet holder, so that the magnet won't sit flush.
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

mrmultifunk, 2022-12-11:
I had this happening as well. What worked for me, was to reheat the insert and press the bulging down with an Allen key.

krankydonkey, 2022-12-12:
What I found worked was inserting the magnet first and then putting the heat set insert in while holding the magnet flush with the side with a ruler

Badnoob-327, 2022-12-13:
I think krankydonkey has a good idea, and we can fix that in documentation (by switching the order and doing magnets before heatets.

Badnoob-327, 2022-12-16:
Next manual has the order of operations switched (magnets in first, then inserts), so this should be fine

ps-bond, 2022-12-20:
> Next manual has the order of operations switched (magnets in first, then inserts), so this should be fine

Is there an issue with breaking the adhesive if that's done?  My usual way of releasing superglued parts is to warm them...

Badnoob-327, 2022-12-20:
I've not had any issues with the superglue getting loose here, if you wish you could try RTV instead of superglue.

ps-bond, 2022-12-20:
Actually I've been using Loctite 480...  I've been using the stuff for a while to glue magnets to prints and have found it more resilient than standard CA.  Probably overkill, admittedly.

nemgrea, 2022-12-27:
fixed via https://github.com/VoronDesign/Voron-Tap/pull/32

Closed 2022-12-27.

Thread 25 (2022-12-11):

Manual errata P29 - "When tightened, the M3x12 head will still be above the rail surface and act as a carriage" - "stop" missing?

ps-bond, 2022-12-11:

Badnoob-327, 2022-12-16:
Thank you, I'll get itin the next rev.

nemgrea, 2022-12-27:
fixed via https://github.com/VoronDesign/Voron-Tap/pull/32

Closed 2022-12-27.

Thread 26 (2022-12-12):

klipper config instruction should instruct the user to remove position_endstop

MapleLeafMakers, 2022-12-12:
When using probe as a virtual endstop, the `position_endstop` setting for stepper_z needs to be removed / commented out.  this should be called out in the instructions.

KiloQubit, 2022-12-12:
It is already called out in the instructions
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

MapleLeafMakers, 2022-12-12:
Apologies, I don't know how I missed that

Closed 2022-12-12.

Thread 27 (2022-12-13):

More information for [stepper_z] section in klipper firmware manual for Tap needed.

kyleisah, 2022-12-13:
Hey there! Small issue, but I think it should also be mentioned that you'll need to remove the `[stepper_z] position_endstop` that *may also* be present at the **bottom** of printer.cfg from previous configuration.

Thanks! ❤️

Badnoob-327, 2022-12-16:
sounds good, feel free to do a pr on that

hyperphonic0, 2022-12-16:
Duplicate of #26 (and it is already mentioned in the instructions: https://github.com/VoronDesign/Voron-Tap/blob/main/config/tap_klipper_instructions.md).

kyleisah, 2022-12-17:
@hyperphonic0 I think you may have misread the issue. Yes, the current instructions tell you to comment out `[stepper_z] position_endstop` but it really should also mention to remove it from the bottom of your config, like what happens when klipper does a `save_config` command to save your new endstop value from before installing Tap. It's there at the bottom where it can be easily forgotten or missed.

Closed 2022-12-17.

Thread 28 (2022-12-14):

Opb961 + electric components fix for manual

artemen, 2022-12-14:
Not all listed opb sensors have color coded wires, for example opb961 has only pins.
Page 13 right hand side picture is really confusing - at first it looks just like the opb sensor view from the button, and if connecting based solely on the looks (very natural given how the rest of the manual is very visual) one can burn mcu.
If just assume that the view is from the bottom it's pretty harmless and just won't work, however if you compare it to the schematic and see that cathode and anode pins are switched in the picture one can assume that it's the view from the top, this will result in short circuiting of the 5v rail on the mcu.
The truth is that page13 picture is neither the top nor the bottom view, but rather a diagram with pins rearranged to make it look neater.
Either include a warning that the picture below is a diagram, or adjust it to make it look as the most useful view- from the bottom.

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

Badnoob-327, 2022-12-16:
Hi, thanks for your comment.  OPB 961 is not a recommended sensor for the Wired option, as it has only pins.  The only wired sensors I have recommended are OPB 991 P51Z , OPB 991 L51Z, OPB 991 T51Z, OPB 991 T11Z

Closed 2023-01-02.

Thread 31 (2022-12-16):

Documentation: X endstop should be shown in different orientation

top-gun, 2022-12-16:
Hi,

I use an X-endstop mounted to the toolhead. In my case it's a KW11, but I saw the same issue with an Omron D2F-L on Discord.

The documentation (page 30) shows the endstop with the latch opening to the bottom. Due to the shape of the XY-joiner, the endstop will not trigger in this orientation. With the endstop mounted in reverse position (latch opening to the top), it will hit the XY-joiner reliably.

I think the documentation should show the endstop with the latch opening to the top so people use the working position.

ditdafivo, 2022-12-17:
For me, even flipping it upside down didn't trigger. I ended up gluing a piece of plastic onto the XY Joint, through on discord someone suggested that bending the lever a little might have been enough.

hyperphonic0, 2022-12-25:
The current Trident CAD shows it in the described orientation.

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

W141-ID, 2022-12-27:
@ditdafivo had/have the same issue. As you suggested I bented the lever which ended up in breaking it's plastic guard, but it seems to work for now.
Just to be clear, lever is still on, just the lever guard has broken off. Now it can make a 45deg turn.

top-gun, 2023-01-12:
Fixed as of Center part R6.

Closed 2023-01-12.

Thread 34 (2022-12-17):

update FAQ regarding hartk pcb

Surion79, 2022-12-17:
In the FAQ, it is mentioned that the hartk PCB must be changed to be compatible, this is not true for the v2.x OptoTap PCB, which does support 24v. It should be mentioned before users with a v.2x OptoTap PCB is scratching their hartk toolhead pcb unnessecarily and producing possible errors/issues in their build

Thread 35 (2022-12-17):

Center void on magnet holders different sizes.

blgli, 2022-12-17:
The circle indentations that were added to Tap_Magnet_Left_r1 and Tap_Magnet_Right_r1, are different depths.

Not sure which is correct but on Tap_Magnet_Left_r1 it is 0.2mm deep and on Tap_Magnet_Right_r1 it is 0.1mm deep, also these STL's are not included in the latest CAD.

Badnoob-327, 2022-12-17:
Hi, thanks for pointing this out.  Those indentations were temporary features to help align the magnets for manual images.  They are not needed and are not in the current CAD, I'll update the STLs to remove them, but there should be no effect on performance.

Closed 2022-12-27.

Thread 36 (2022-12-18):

X-Rail mount step doesn't say it's mounting to X-Rail

mobilemcclintic, 2022-12-18:
On Page 29, the manual shows putting (4) M3x6 BHCS into the holes that mount to the X-Rail carriage.  Right after that, it notes about installing the X end stop magnet.  In my mind, I'd install the magnet when the assembly is off the machine, so I was dropping screws as I was glue and pressing the proximity magnet in.

Maybe it should have a picture of the X-Rail carriage in the image so it's explicitly shown that it is being physically connected to the machine.  Maybe it's just me.

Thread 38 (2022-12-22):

Chamfer in hole

Lelle79, 2022-12-22:
I have a chamfer in the angled holes for bolting "tap upper" to "tap front". is that supposed to be there? the slicer picture is upside down. sorry for that.

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

nemgrea, 2022-12-27:
that feature is to prevent the slicer from creating overhung bridges in that area. your image shows the part being sliced in the in correct direction. in real life the parts bolt up just fine, the funky cad feature is just to force a specific behavior from the slicer

Closed 2022-12-27.

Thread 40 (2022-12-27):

Consider increasing depth of solder blob relief in Tap_Upper_PCB CAD from 1mm to 2mm, to reflect actual pin length/needed relief

nearctx, 2022-12-27:
Currently the TAP_Upper_PCB_r2 part has a 1mm deep relief for the pins and solder joints of the JST connector on the OptoTap v2.1 PCB so the PCB can sit flush when screwed down, however the pins of the spec connector(S3B-PH-K) in actuality stick out 1.8mm from the bottom of the PCB. Extending the depth of the relief to 2mm should resolve this issue.

Of course it is not difficult to just trim the pins down a little before or after soldering, but extending the relief to 2mm is a small change that would make assembly easier, and eliminate the opportunity for issues arising from the PCB being installed incorrectly due to the pins blocking it from sitting flush.

The measurement of the pins protruding 1.8mm from the PCB bottom is taking the specified PCB-side pin length of the JST connector, 3.4mm(Page 2 of the JST PH connector datasheet - see below for screenshot and link), then subtracting the nominal PCB thickness of 1.6mm, = 1.8mm protrusion. So a 2mm relief should be enough to account for any potential variance in pin length/PCB thickness.
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
https://www.jst-mfg.com/product/pdf/eng/ePH.pdf

I have also personally experienced this issue with the solder relief being insufficient with the current 1mm depth, and I have physically measured the pin length protruding to indeed be about 1.8mm as well.

Also I'd like to take this opportunity to say thanks to everyone who has contributed to Tap, its awesome!

raymondh2, 2023-01-02:
@Badnoob-327 @tanaes

blownupp, 2023-02-26:
I'll second this - I had to trim the pins down a little bit to install the PCB, but it isn't critical either...

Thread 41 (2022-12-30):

One null too much in the description

vjeko2404, 2022-12-30:
Hi, just wanted to point out that 4 micrometer = 0.004mm

the description says 0.0004mm.
This issue can be closed.

btw. the sensor works very good! I already got my clicky replaced with the tap.
Very good job as always!

thank you!

vjeko2404, 2022-12-30:
Nvm, didnt notice the 0.4um. Still highly unlikely and strange way of

Closed 2022-12-30.

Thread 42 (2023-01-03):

U2 AP63205 Can suffer catastrophic failure under some circumstances

pii100, 2023-01-03:
Multiple reports of U2 releasing magic smoke in discord see https://discord.com/channels/460117602945990666/1058146062457643029

Suspected instability on Vin during power up causing oscillation leading to failure.

tanaes, 2023-01-03:
We are currently tracking down the issue. This affects *all* V2 (24V-compatible) boards. **IT IS DANGEROUS** in that it can lead to an uncontrolled short in the failed regulator, so it is advised that people discontinue use of these boards immediately. Although we haven't heard of any failures yet when operated at 5V, it's completely possible that it could still happen, so we can't recommend using them as-is at 5V either at this time.

The reason we didn't catch this failure in testing is that it seems to be heavily setup-dependent, potentially due to variation in the electrical characteristics of the power connection. Thus, none of the ~250 boards I assembled and tested ever popped a regulator at my bench, but some of those same boards had their regulators fry when connected to someone else's printer.

Unfortunately, that also suggests that these boards as-is are right on the edge of whatever instability causes the failure. Thus, even if you've installed one in your machine and it has been working fine to this point, it may still fail at some point down the line. I would not consider keeping one of these PCBs on my machine, personally.

I will be posting a full write-up here when we've fully diagnosed the issue, and in the meantime we are also working on a couple different approaches for board revisions that we will be testing ASAP.

Please follow the linked thread in Discord for additional info.

tanaes, 2023-01-05:
# Update 4 Jan

Thanks to the incredible help of a bunch of talented and generous people in the Voron Discord, we have a candidate for a root cause of the failures as well as a corresponding interim solution that should at least *reduce* failures on V2.1 boards.

## Root cause candidate: inrush voltage spike

The vast majority of failures seem to occur on initial powerup of the sensor PCB, and so far all reported cases have happened when connected to 24V rather than 5 volts — especially when 'hot plugging' the board into an already-energized power rail.

What appears to be happening is that inrush current (as the 22µF input decoupler capacitor is initially charged) combines with inductance in the power lines to cause a transient voltage spike at the Vin pin of the switching regulator IC. This happens because the electromagnetic field produced by current flowing through the power wires stores some amount of energy; once the input capacitor charges to 24V that electromagnetic field begins to collapse, dumping the energy back into the capacitor in the form of higher voltage.

A Discord member demonstrated this using an LTSpice current simulation, using estimates for resistivity and inductance of 2m long 24 AWG power wires:

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

Discord member Ran_K updated this with a more realistic model incorporating DC bias in the actual input capacitor used, and showed that this could lead to even higher voltages, briefly exceeding 50 V.

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

They were able to subsequently demonstrate actual peak voltage of around 54V at Vin on an oscilloscope using a V2.1 board:

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

I was able to replicate this phenomenon on my own scope, in my case reaching a peak observed voltage of around 43V when hot-plugging into a 4A current-limited power supply set at 24V:

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

By contrast, hot-plugging a 5V input gave a maximum voltage spike of under 10V:

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

These numbers seem to fit reasonably well with the observed patterns of failure that have been reported. The AP63205 regulator used on the V2.1 PCB has a datasheet maximum of 40V for transient spikes on Vin, which given the variation in actual electrical characteristics of peoples' specific setups (including likely lower inrush when not hot-plugging), helps explain why only a minority of boards have been reported as failing — as well as why setups that toast one board seem more likely to toast subsequent boards, as well.

## Proposed interim solution

Adding a very small amount of series resistance to the +24V power connector may damp the inrush current sufficiently to reduce the transient voltage spike to safe levels without compromising the performance of the sensor. To test this, I made a wiring harness with a 1Ω wire-round resistor in-line on +24V wire.

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

On the scope, using the same testing setup as above, you can see that this dropped my maximum voltage spike from 43V to about 30V — well under the datasheet maximum for the IC.

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

This setup only marginally reduced the steady-state voltage at Vin, with only an 18 mV drop with a supply of 5V:
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

This suggests that using a 2.2Ω resistor would be an even better option. I didn't have a 2.2Ω wire-wound on hand, so I made another test harness using a small SMD chip resistor. (A thin film resistor is a poor choice for this in actual use, more on this later; however, it worked fine for a quick test.)

In the linked YouTube clip, you can see that repeatedly hot-plugging a board using the in-line resistor works totally fine, while the board without the in-line resistor fries after just a few tries:

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

### How to modify your wiring harness

**This is a proposed band-aid, not a solution. Please be careful. If you have any doubts, there are a number of alternatives switching mechanisms for Tap available.**

Use a 2.2Ω wire-wound resistor. It is important to use a wire-wound resistor rather than the more common thin-film resistors because they have better power pulse characteristics. The resistor will briefly see a high-wattage pulse at powerup (perhaps  1-200W over 10 µs), and this can quickly break down thin-film resistors.

Make sure to tin the wires and resistor leads before soldering them together:

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

Then heat shrink over the exposed leads to give them some strain relief and protection from shorting:

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

## Other potential issues for revision

In addition to dealing with inrush on-board, we are looking at making some additional improvements in a revised board as soon as possible. These changes may include reverse polarity protection, improved regulator tuning, and broader sensor compatibility.

tionebrr, 2023-01-08:
Hello folks,

The optical sensor open collector is directly exposed to that kind of issues too. It's risky. I would drive the line with something else than the sensor itself. Could be a mosfet (or a PNP) and a dedicated pullup, or an ESD protected logic buffer, whatever is the cheapest that fits the bill and the board. A simple resistor in serie would already give some protection.

For the VIN surge, the solution you implemented here is a simple RC filter which is the cheapest way to deal with it. A TVS diode would be a more serious protection.
Also, if you put a fuse before the TVS, that fuse will get triggered in case of reverse polarity. It's not a perfect solution because of the fuse trip time, but this could be calculated and tested.

skygrip, 2023-01-10:
Hi All,

What was the logic around using a Switch-mode power supply for whats effectively a 50ma optical switch? Surely a jellybean linear regulator like the LM7805 would be simpler, cheaper, and avoid any chip-shortage related supply chain issues. Linear regulators don't need high value decoupling capacitors, and have orders of magnitude better transient response.

tionebrr, 2023-01-10:
I thought that too @skygrip

tanaes, 2023-01-10:
Initially to allow operation from 5-24V while staying within the 4.7V datasheet minimum voltage for the OPB971 sensor. Also while 50 mA doesn't sound like a ton, using an LDO to drop from 24V still means dissipating close to a watt on a very small PCB in a hot chamber. That said, i've ordered an LDO-based prototype as well for evaluation in the next round.

These issues are being discussed extensively on Discord, so I'd appreciate if you'd ping me there in the #24V OptoTap Board Troubleshooting thread in the #voron_tap channel so we can keep the signal:noise ratio on this issue high for people. Thanks!

tionebrr, 2023-01-10:
The Voron Discord is mostly a user place. It's very noisy. Github is more practical for people who wants to contribute imho.

There are optical sensor with forward current as low as 5mA. The board as of today may be too small for the protection and signal conditioning components anyway.

JendaDH, 2023-02-08:
Hi, can't we just put bi-directional $1 TVS diode on the input and save the IC and other components from the peak voltage?

tanaes, 2023-03-03:
# Issue resolution

After some extensive testing and lots of input, PR #53 should resolve this issue.

## Testing

To help with stress-testing the circuit, I put together a test rig using a rotary contactor. This allowed me to hot-connect up to eight boards in quick succession, and rack up thousands of individual tests across dozens of prototypes. (This also took a few iterations -- the first attempts, which connected the boards in parallel, didn't reliably reproduce the failures.)

[[Test setup and 5V]](https://imgur.com/e4ggTBc)

Using the test rig on the V2.1 boards, you can see the inrush voltage spike (and ringing) at 12V supply, with spike peaking at around 24V:

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

### Testing original circuit

And at 24V, the inrush spike peaks at around 52V and immediately causes a short in the regulator, causing the power supply to go into current-limiting mode:

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

Using this setup I was able to reliably fry the V2.1 boards in relatively short order. (Although it's worth noting that some individual boards survived a few dozen attempts before blowing.)

[[Frying boards]](https://imgur.com/axee4tO)

### Testing original circuit + series resistor

Using the same setup, a 2.2Ω series resistor dampens the circuit enough to basically eliminate the voltage spike.

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

I was unable to fry any of the original boards using the 2.2Ω in-line resistor.

[[Testing in-line resistor]](https://imgur.com/cd0fLqe)

### Testing a revised circuit

The revised version of the circuit has a number of changes. For a full run-down, see the change log in the Readme. Two are especially relevant to this issue: 1) adding a polyfuse and 2) Schottky barrier diode into the Vin path.

The Schottky diode protects against accidental reverse polarity connection, as might happen if one were to accidentally swap Pwr and Gnd leads when connecting. Before, that would cause the regulator to immediately short.

The polyfuse does double duty. First, the low (1-6 Ω) resistance under normal operating conditions is enough to fully damp the system, eliminating the voltage spike.

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

Second, in the case that something downstream did short, the polyfuse will increase resistance and limit the amount of current flowing through the device.

I have been unable kill any boards using this protection circuit:

[[Updated circuit testing]](https://imgur.com/RegJSfE)

### Real world release candidate testing

To gather some real-world testing, I sent about 20 release candidate boards out to testers to try on their machine. No one has seen any failures yet (despite some aggressive attempts), and the distribution of responses suggests that performance should be about the same as before.

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

## Design considerations
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
tionebrr, 2023-03-04:
@tanaes and all the contributors, amazing work guys !

Closed 2023-03-03.

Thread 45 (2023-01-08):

PCB needs EMI and grounding improvements (and other remarks)

tionebrr, 2023-01-08:
I checked the project yesterday.

Here are some recommendations; those will improve the EM susceptibility and characteristics of the board:
- Reduce the ground planes margin to near the manufacturer capabilities (0.127mm for JLCPCB -> 0.15-0.2mm).
- Add vias to stitch the ground planes together
- Make the board such that all traces are routed inside a ground plane.
- EMC profile of a 2-layer board tends to improve when the board gets thinner. Avoid using the standard 1.6mm board.

Those are some ameliorations on the design:
- The copper layer should be retracted from under the screws. Humidity will creep under a damaged soldermask. That kind of details make boards work 20 years longer for free. ;)
- The AP63205 datasheet states that the 220nF C2 could be 100nF 0603. Not sure what's going on here, I may miss something, but if it works at 100nF, go for it.
- The switching node of the AP63205 is very compact (L1 very close the the SW pin), which is perfect. I would use a small copper pour to connect this node it a bit better.

Some EDA tricks:
- Name your schematics nets. It's making the routing and the editing way easier.
- You don't need to create a plane for TOP and BOT copper in kicad, you can have a single plane pouring on multiple layers.
- Lock the positions of all mechanical components. I shouldn't be able to move the screws holes for example ;)

I've joined a zip file with some quick modifications to the design you can look at. I have some spare time if you need any help for design and testing. ;)
[Tap_Photosensor_PCB_v2_modified.zip](https://github.com/VoronDesign/Voron-Tap/files/10367618/Tap_Photosensor_PCB_v2_modified.zip)

TorbanP, 2023-02-14:
I just incorporated your changes into a board that also integrates a TVS. I like the comment on copper layers under screws; I haven't heard that one before. The other changes were perfect (switching node) , although sticking a tvs was a bit tricky due to spacing. I just ordered 10 and will dial in the TVS
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

tionebrr, 2023-02-21:
Hello @TorbanP , that's looking way better already!
Closing ;)

Closed 2023-02-21.

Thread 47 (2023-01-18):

Broken link in Manual

MapleLeafMakers, 2023-01-18:
On page 5, The github link for the STLs is incorrect, it points to https://github.com/VoronDesign/Voron-Tap/STLs instead of https://github.com/VoronDesign/Voron-Tap/tree/main/STLs

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

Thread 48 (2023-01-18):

Toolhead mounting screw clearance seems to be wrong

ressu, 2023-01-18:
Yes, a very very minor thing. I think in the manual, on page 25, it's stated that the toolhead holder screw needs a 2.5mm clearance. But considering that the mount on SB parts that slots into those screws is ~3.3mm wide the correct value should be 3.5mm.

With 3.5mm clearance the ends of the screws also seem to match how the part was designed and the ends of M3x16 screws don't dig into the plastic on `Tap_Upper_*` part.

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

claudermilk, 2023-01-23:
I ran into that as well. I set the screws to 2.5mm as the manual directed, but had to back them out a bit to get the SB hotend mount to fit.

Badnoob-327, 2023-01-25:
I'll take a look, thanks

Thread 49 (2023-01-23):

Upper/Front attachment causes large warp

GaryBoone, 2023-01-23:
On page 25 of the manual, the `upper` is attached to the `front` with two M3x20 diagonal screws. In addition, the two M3x16 mating screws also hold the parts.

Later, the extruder is attached to the `upper`, while the hotend is attached to the `front`. This means that any imperfections in the angle of the `upper` and `front` to each other make the extruder and hotend out-of-plane to each other.

This warp does not become apparent until the fan assembly is fit, when force must be applied to re-align the extruder and hotend so that the fan should mates correctly and can be bolted.

The problem, I believe, is that the angle between the parts is affected by the diagonal and horizontal screws. Because the diagonal screws are at a 45° angle wrt to the horizontal screws, they pull the parts out of alignment.

After discovering this issue, I rechecked and filed the printed parts to ensure that they mated correctly. While this improved the collinearity of the extruder and hotend, it did not solve it completely. Also, it is nearly impossible to judge the alignment with just the parts.

The problem is visible in Kapman's Basement Workshop's [TAP video](https://youtu.be/5FaUZ4w1jmI?t=1070) at 7:50. When he tightens the lower screws, a gap appears at the top of the fan shroud.

The result of the warp is that aligning the bolts for the fan shroud is made more difficult, as well as causing internal stresses in the system when it is forced to fit for final assembly.

Suggestions:
• Redesign the parts to correct the issue.
• Until then, add a note in the manual to reduce confusion when users notice the misalignment. How much of a gap between the extruder and the fan shroud is acceptable? How much force should be applied to make the extruder and fan connect?

Badnoob-327, 2023-01-25:
we are seeing some cases of this and were all the way back to beta. Thought we had fully addressed it, but I can see its still happening in some cases.  I'll take another look, thanks.

Redwish89, 2023-03-26:
Any updates on this? There seems to me more reports on the Voron Discord without a clear cause or solution to prevent/fix the gap.

leeeboo, 2023-07-03:
I have the same issue. I have made 3 taps and stealthburger, all have this issue.

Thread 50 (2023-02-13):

Cracks on top bolts on [a]tap_center_r6

SinisterRj, 2023-02-13:
Trying to debug some ressonance issues on my printer I was checking the overal boolts torques and accidentaly break this piece. But looking at it, I felt that this part is verry week at this point, with only 3 walls from here the bolts make contact do the end of the part. I was able to increase this number to 5 without reducing the clearences to the other parts. And in my modification I was abble to cincundate the entire rail carrige, also increasing the stiffness of the part a little bit. The new part is printed and it is working on my printer.

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

raymondh2, 2023-02-21:
Hi. Could you please provide what material and color the part was printed in?

SinisterRj, 2023-02-21:
It was printed in Dental White ABS MG94 from GTMax3D (a brasilian 3d printer manufacturer and one of the best filaments in Brazil)

nemgrea, 2023-03-14:
unfortunately white filaments are known to be less robust compared to their equivalent darker colored counterparts due to the colorants needed for getting white filament.

SinisterRj, 2023-03-14:
Yes, I know. The new part I printed on black. But, anyway, it gave me an opportunity to improve a weak point of the part.

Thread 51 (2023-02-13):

LDO MGN12H Carriage End Caps Not Flush - Possibly Others

Darkstar77, 2023-02-13:
EDIT 2: 20230503: R8 should solve this. If you're experiencing this, please print and install the R8 revision of TAP, which includes actual clamps for the belts, which should completely eliminate this.

R8 is very similar to how I was trying to solve this myself, and am quite happy to see I was going down a similar path to solve it. I'm going to abandon mine, and suggest you just download the R8 parts.

EDIT: For anyone finding this, I have some revisions on the center, and some directions on assembly here that should help resolve this for most people: https://github.com/Darkstar77/Voron/tree/main/TAP

My 2.4r2 is a LDO kit. The LDO kit MGN12H carriage has a ~0.55mm drop from the main carriage body to the end caps. It seems like a pretty small amount, however I've now had my belt slip and strip out the belt retainers on the TAP centre piece 3 times in one day. I was taking it apart to resolve a loose MGN9 rail issue, and had printed the R6 revision of the centre.

I decided to remove the centre assembly to replace it with the newer revision. I noticed that the tooth immediately beside the hole for the belt to pass through had stripped off, with damage to it's neighbor. This was the upper belt, and only one side of the centre was effected. This centre had about 200 hours of printing on it.

I reassembled it with a brand new centre, and on tensioning the belts, the upper belt again slipped. When I took it apart, the teeth were stripped in the exact same way. There appears to be no damage to the belt.

I printed a third centre, added some 1mm foam to the end caps of the LDO MGN12H carriage, and carefully re-assembled it. Tensioned the belts, and it looked good. Re-assembled the print head, and started a print. It got about 10 minutes into the print, and the belt slipped again. Same deal, the tooth immediately beside the pass through hole was stripped off for the upper belt on one side.

I saw at least one user with the same problem on Discord, with the same non-flush end cap on their carriage too. This was not an LDO carriage. When I inspected the carriages on my switchwire, I noted that the end caps were not flush on those carriages either. Those were generic china rails. I'd like to blame user error here, just say I was too rough, over tensioned the belts, etc.. This third centre I printed today, when I assembled it, I was very gentle with the assembly, and the tensioning. If anything, the belts were slightly under tensioned.

0.55mm doesn't sound like a lot, but it is apparently enough to allow some wiggle room for the belt to move, and as a result it is really easy to strip the belt retention. Once the tooth closest the pass through hole is gone, it is no longer able to hold the belt, and it slips. That essentially means that a single tooth is properly engaging the belt in this scenario, and nothing else is really retaining the belts. This makes the whole thing very easy to strip out and fail. The LDO rails are widespread, and by no means the minority.

Darkstar77, 2023-02-13:
I designed and printed a tiny spacer for my carriage, which makes the endcaps flush with the rest of the carriage. So far, new centre is installed and tensioned, and nothing is looking off, no belts slipping. I believe this is definitely an issue in respect to the belt retention on the X carriage.

jjfs127, 2023-02-16:
Same LDO 2.4r4 kit with same rail and consequently same problem. My solution was to extend the ridges of the rail mount higher to apply more pressure to the belt against the rail bed. I also reported this problem in the Voron tap discord channel. I hope this issue gets more traction and an official fix is provided.

@Darkstar77 would you mind sharing the spacer?

Darkstar77, 2023-02-17:
>

@jjfs127 I had been meaning to setup my personal repo, so here you go: https://github.com/Darkstar77/Voron/blob/main/2.4/stls/TAP-LDO_MGN12H_Spacer.stl

It's challenging to print. 0.1 on the first layer, and 0.1 layers. I had to give a little extra squish and width to get the first layer to hold together on the thin sections. The thin portion is really just to help align everything, once you tighten the TAP centre down, it's not going anywhere.

nedi89, 2023-02-21:
I‘m having the same problem. Vivedino carriage. I’ll try to see if it works with spaces but I hope voron team comes up with an official solution.

Darkstar77, 2023-02-22:
@nedi89
> I‘m having the same problem. Vivedino carriage. I’ll try to see if it works with spacer but I hope voron team comes up with an official solution.

You might give that spacer I linked a go. Not sure it will fit that rail, but it's solved my issue for the time being. It's tricky to print, because it needs a 0.1 first layer, but otherwise is a 3 minute print.

I've been looking at the issue, and the only thing I can think of would make the centre thicker, which is not great. Essentially moving the holes for the belts to the inside of the 4 screws holding the centre to the carriage. This would clamp the belts firmly against the steel of the carriage, with clamping force more evenly distributed, much like the original carriage. The down side is clearance around the MGN9 rail and carriage, and why I believe it would add additional thickness to the centre and the overall TAP. Not sure folks want to loose another 2 ~ 3 mm on Y.

nedi89, 2023-02-22:
I went back to euclid and cw2, I'm going to wait this one out, hopefully Voron team comes up with a solution, don't want to buy a whole new rail because of the TAP.

Darkstar77, 2023-02-24:
Welp, after about 30 hours of printing with the spacer in place, I am back to square one, because my belts are slipping again. I got through a bunch of PLA prints, without issue, but when I went to do a long ABS print, chamber up to 55C, the belts slipped again. I haven't taken it apart, but I can guess what I will find, which will be teeth ripped off again. This needs to be addressed.

jjfs127, 2023-02-24:
@Darkstar77 You can give my mod a go. I haven't seen mine slip. I extended the ridges higher, now,  whether they apply too much pressure on the belts, I'm not sure.
[[a]Tap_Center_r6_modified_ridges.zip](https://github.com/VoronDesign/Voron-Tap/files/10828451/a.Tap_Center_r6_modified_ridges.zip)

nedi89, 2023-02-24:
Yeah, I tried your spacer first, it doesn't work for me. I like the idea of TAP but I personally think this mount design is not really thought through. There is just not enough force pushing those belts against carriage, the holding point is too far out on the edges, belts are going to slip sooner or later, or you have to keep them fairly loose. Best solution would be to place those ridhes closer to the middle, where you can really apply some force with those 4 screws but to be honest, I don't see how's that even possible.

Darkstar77, 2023-02-25:
@jjfs127 I tried your part, it failed on the first print, same deal. I see what you did though, and how you did it. Extruding the faces on top of the teeth. It's a good idea.

I've taken the CAD for the centre, and did some work on it. Similar to yours, but I took the time to re-sculpt the teeth to match their original profile, as well as increase the overall height of the surrounding shoulder that interfaces with the end caps. I am hoping that increasing the should by 0.2, and the teeth by 0.4, that will take up all the slack the end caps on the LDO carriage have, and will work. Printing it right now, and will be installing it later. If it works, I will upload it to my github, and link it.

jjfs127, 2023-02-25:
@Darkstar77 Sorry to hear it didn't work but I think you're on the right track. I thought of what you'd did alas my cad skills are novice at best. Let me know how it goes..

Darkstar77, 2023-02-25:
@jjfs127 here is the difference between the original R6, and what I've done.
https://github.com/Darkstar77/Voron/raw/main/TAP/OriginalCentreNewCentre.png
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
x-c-dog-x, 2023-03-06:
Yeah, not really in favor of having the belts push down any more on the endcap wipers. Surely, will cause other issues. Still, at this point, I went back to using the stock Center and cut a couple strip spacers of a HDPE plastic lid and attached them with double-stick tape (just to hold them during assembly) on top of the endcaps. So far, after about 60 hours of enclosed printing they're hiolding up. Now I see another issue that will probably invole extrusion backers to help keep things in line after everthing heats up. WIll have to look at 6.2 when I get the chance.

nedi89, 2023-03-06:
I printed and installed the 6.2 centre , so far it's doing great after around 20 print hours. I'm printing only ABS so it should really put it to the test. I'll keep you updated.

nedi89, 2023-03-08:
Just an update, after around 40 print hours, my belts slipped again and I got a nasty layer shift. I dissasembled the whole thing and went back to old cw2 mount system with euclid probe and I think this time it's for good. I im no mood to assemble and disassemble every couple days.

Darkstar77, 2023-03-08:
@nedi89 were the teeth damaged where the belt slipped?

I'm beginning to suspect that the only way to really fix this is going to be to make it thicker by about ~3mm, so the slots can be moved inboard and come out by the rail. That way the clamping force would be more even, with a large engagement area. It would place the belts inboard of the screws... I'm going to look into that as an idea.

nedi89, 2023-03-08:
@Darkstar77  yes the teeth are damaged, broke off basically, the ones that didn't broke were deformed, was just waiting to happen. I should say that after initial belt tightening after assembly, I didn't try to retighten it or anything. Yeah, i also replaced my Vivedino X rail and carriage with a genuine HIWIN ones, because Kapman mentioned he didn't have any issue with the TAP on his HIWIN.

jjfs127, 2023-03-08:
I bit the bullet and bought another mgn12 rail. I went for a CNA rail as per the BOM. I will be going back to the standard piece and will try it in ASA-CF, hopefully with better results.

macmanluke, 2023-03-18:
Defintely had issues with this on my LDO rails (although less since i made sure to loops the belts fully around)
Just had the outer bits break off so will try this version.

sf-pfm265, 2023-04-19:
@Darkstar77 any update on your v2 design? I'm running an LDO Trident with Klicky PCB and I'm thinking of migrating to Tap.  I could switch out my rail to a different manufacturer as some here have done, but if your V2 fix is working, then I'll give it a try.

Darkstar77, 2023-04-28:
> @Darkstar77 any update on your v2 design? I'm running an LDO Trident with Klicky PCB and I'm thinking of migrating to Tap. I could switch out my rail to a different manufacturer as some here have done, but if your V2 fix is working, then I'll give it a try.

The latest version, which I've been running, is on the linked github. It's versioned 6.2, and so far it's what I've been running. I have to admit that I purchased a CNC TAP kit now, so I will be replacing it eventually. So far my version of the TAP center has been holding up well. That said, it still failed for another person in the same way. I have been tinkering with a mod that routes the belt path under the screw that secures it to the MGN12H carriage, to apply more clamping force, but so far my attempts at that add about 4mm of thickness to the part, and you lose ~4mm on Y. I'm not happy with that.

DrFreeman001, 2023-05-02:
Same problem here. LDO Kit.

macmanluke, 2023-05-02:
V8 is out now which fixes this problem (as does cnc tap)

Darkstar77, 2023-05-03:
> V8 is out now which fixes this problem (as does cnc tap)

Looked it over, and yes, that is similar to the direction I was going in to try to solve this. Pretty happy to see that. Updated my original post to direct people to the R8 version.

Badnoob-327, 2024-06-27:
Closing this as fixed with R8

Closed 2024-06-27.

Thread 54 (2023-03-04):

RTV silicone doesn't work to hold magnets in carriers

fwiffo, 2023-03-04:
RTV doesn't adhere well to the ABS and doesn't adhere at all to the magnets. The reference should be removed from the manual.

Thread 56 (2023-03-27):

Additional head assemblies

trampas, 2023-03-27:
The head assembly instructions appear to be for a V6 head, many kits ship with StealthBurner and Revo nozzle.  It would be good to add into the documentation instructions on how to identify parts you have and include instructions for alternative heads.  I would do this myself and add a pull request but the source for PDF is not in git.

raymondh2, 2023-03-27:
We don't have instructions included with tap for any toolhead.

Closed 2023-03-27.

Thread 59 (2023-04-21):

jlcpcb - Incorrect Part Placement?

thijstriemstra, 2023-04-21:
hi @tanaes I submitted the bom and placement files for an order at jlcpcb (my first) and uploaded the files provided in https://github.com/VoronDesign/Voron-Tap/tree/main/OptoTap/Tap_Photosensor_PCB_v2/jlcpcb/production_files

They came back with the following issue though, so it seems the PCB placement is off or I did something wrong..

Their feedback:

> Since we are not so sure about the polarities of the components D1 are correct or not. Could you please kindly check if the polarities and placements of the components are correct in the below picture? Is it okay to proceed with production?

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

thijstriemstra, 2023-04-24:
> Since we are not so sure about the polarities of the components D1 are correct or not. Could you please kindly check if the polarities and placements of the components are correct in the below picture? Is it okay to proceed with production?

I opened the `Tap_Photosensor_PCB.kicad_pro` file in KiCad 7.0 and it shows the following schematic for D1:

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

I guess that'll be enough info for them to answer their question about D1, but I'll also include a [link to the kicad files](https://github.com/VoronDesign/Voron-Tap/tree/main/OptoTap/Tap_Photosensor_PCB_v2).

tanaes, 2023-04-24:
The positive terminal should be in the upper left of the footprint in that picture — their “corrected” part is upside down.

thijstriemstra, 2023-04-29:
thanks for the feedback @tanaes. they returned with:

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

tanaes, 2023-04-29:
That is incorrect -- D1 should be rotated 180°. Pin 1 should be in the
upper right corner, as denoted by the corner mark in the silkscreen.

On April 29, 2023, Github Notifications ***@***.***>
wrote:
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

thijstriemstra, 2023-05-04:
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

thanks @tanaes, they came back with this, and it looks ok now right?

tanaes, 2023-05-04:
That is correct!

On May 4, 2023, Github Notifications ***@***.***> wrote:
>

> thanks @tanaes <https://github.com/tanaes>, they came back with this,
> and it looks ok now right?
>

—
Reply to this email directly, view it on GitHub
<https://github.com/VoronDesign/Voron-Tap/issues/59#issuecomment-
1534679256>, or unsubscribe
<https://github.com/notifications/unsubscribe-
auth/AB7ISADPAQJN5DDBKJCORGLXEONUNANCNFSM6AAAAAAXGGLK3I>.
You are receiving this because you were mentioned.Message ID:
***@***.***>

thijstriemstra, 2023-05-05:
thanks for the help, the production started. how can we prevent this from happening to other users, it seems the jlcpcb .zip files in the repository produce incorrect jlcpcb instructions? can they updated? im not sure how because  i don't see an export to zip function in the jlcpcb interface..

tanaes, 2023-05-05:
initially I think JLCPCB had incorrect pin numbering for this part in
their system, so what would happen is the original automated placement
would be correct but then they would go back and manually 'fix' it to be
backwards. My guess is that they have updated their database but that
has broken the rotation for that part in the file. I will need to re-
export and check again.

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

—
Reply to this email directly, view it on GitHub
<https://github.com/VoronDesign/Voron-Tap/issues/59#issuecomment-
1535589639>, or unsubscribe
<https://github.com/notifications/unsubscribe-
auth/AB7ISAGNZ733DGNNNSPNBK3XERJ3ZANCNFSM6AAAAAAXGGLK3I>.
You are receiving this because you were mentioned.Message ID:
***@***.***>

thijstriemstra, 2023-06-13:
looks like this was fixed in https://github.com/VoronDesign/Voron-Tap/commit/e783ce8710ebc401b4b872ef84dd3216f443cf81, thanks!

Closed 2023-06-13.

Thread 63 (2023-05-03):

Continue to support MGN9H

jueank, 2023-05-03:
I would like to see the team continuing to support MGN9H rails (at least a single rail) instead of only MGN12H. There is still a fairly large group of Voron owners using MGN9H. Similarly to support a variety of toolheads (like still E3D V6 and more), MGN9H should not be forgotten. I don't see a technical reason to make such a hard cut but only because of not wanting to spend the effort.

tnibler, 2023-05-03:
> but only because of not wanting to spend the effort

Which is a totally valid reason of not doing work for free, is it not?

jueank, 2023-05-03:
Yes, perfectly valid. But I clearly vote for the continuation. In my opinion, this is an example of relativism in its purest form, because you could question any topic if you put the voluntary effort against it. Stop working on Vorons. it's work for free. You could stop it immediately. How would you want to argue against it? I don't think we should start a fundamental disussion about MGN9H vs MGN12H. The lead developers should just think about it and know that there are users interested in TAP but otherwise happy with MGN9H. Yes, I know, you can do mods on your own. But this is far different from being officially supported and this is exactly what I'm asking for here.

JanB97, 2023-05-03:
I am not as in to the current voron team, but could you not do a MGN9 mount and make a pull request?
Maybe they will upstream your design.

Clearly the message is that they are not happy with the mgn9 design and don't want to support it so people get rid of it.

Badnoob-327, 2024-06-27:
I don't think it is possible to use MGN9H rails in tap, without compromising the design.  I did try early on (ad I also had a MGN9 dual rail).

Closed 2024-06-27.

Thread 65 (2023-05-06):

SB issues when using CW1 Mod

ChrisWhite1985, 2023-05-06:
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

Protruding Button screws seem to push out the extruder holder. The bottom buttons do nothing in this case so they had to come out as leaving them in means the M3x50 screws are not long enough to reach the tap bracket.

Mod from RepRapster3D makes the CW1 Motor Plate fit TAP but SB Hotend Holder doesn't look right.

ChrisWhite1985, 2023-05-06:
Noticed the hotend part carve notes in the manual, will check / modify the part to see if this makes a difference.

ChrisWhite1985, 2023-05-07:
Removed plastic on hotend printed part that clashed with Tap as per the manual.

Closed 2023-05-07.

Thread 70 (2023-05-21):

Questions Regarding the Use of Voron-Tap

leeeboo, 2023-05-21:
Hello,

I've recently started using Voron-Tap and I have a couple of questions that I hope the community can help answer.

1. Does residual filament on the nozzle affect the z-offset? If so, how can this issue be addressed?
2. I tend to apply adhesive on the print bed during printing. Will this have any impact on the printing process?

I would appreciate any insight or advice on these matters.

Thank you!

TheFuzzyGiggler, 2023-05-25:
1.) It will change your z-height but since the tap sensor is relative anyways it shouldn't affect it much unless the residual filament gets dislodged while running your homing macro. What I mean by relative is, that the Z height will be offset for every probe as long as that residual filament is attached. You should be rehoming between prints anyways so it shouldn't be a major issue.

2.) Nope, except you might get some adhesive on the nozzle where it taps the bed during probing. But I don't think that will be an issue really.

Closed 2023-05-25.

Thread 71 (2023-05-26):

Incorrect bolt length for rail

Furcube, 2023-05-26:
Manual specifies M3 6mm. 8mm and 12mm With part which have old version of [a]_Tap_Center_r8.stl.
8mm and 12mm bolts are too short for current version.

In step file bolt lengths are 6mm, 12mm and 16mm.

Martorias, 2023-07-20:
It's mentioned in the r8 errata; https://github.com/VoronDesign/Voron-Tap/blob/main/Manual/R8_errata.md
I didn't find this until I started building it as well so perhaps it's time to update the regular manual.

widarlein, 2023-09-01:
Yup, as @Martorias said. It's in the errata. There's no mention of the errata in the main readme though, just a link to the manual so I found it quite confusing. I ended up melting the heatset inserts farther into the plastic yesterday when the bolts didn't reach and I hadn't read the errata.

I also missed the other steps in the update but those weren't irreversible so I could take it appart and fix.

The manual should probably be updated or there should be clearer links to the errata at least

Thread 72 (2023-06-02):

Sensor compatibility

proxyissues, 2023-06-02:
Some optical sensors EE-SX398 do not correctly trigger due to the SIG pin voltage only flipping between 1.4V and 0V.
This appears to be dependent on Sensor and the floating voltage that the pin will sit at being not predictable and may affect other recommended Sensors.

The improvement would be a 1K or 10K Resistor connecting 5V to SIG so that the SIG pin is held high @5V until the sensor pulls it to GND indicating a change in state.

I've verified this on my Tap board connected to SB2040 HV compatible pin (GPIO25) and it is now a stable 5V or 0V signal.

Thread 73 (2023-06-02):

Recommend adding thread locker to M3 SHCS attaching linear rail to center section.

metzgarj, 2023-06-02:
After about 50 hours of printing I noticed the entire print head was coming loose.  After disassembly I found the three M3 SHCS attaching the linear rail to the center mounting structure were all coming loose.  I've gone back and added blue Locktite to each of these screws to fix the problem.  I would recommend adding this to the assembly manual in future revisions.

Badnoob-327, 2024-06-27:
Sorry for the very late response. R8 redesigned this part to improve this.  I don't recommend threadlocker in plastic parts, many threadlockers are not compatible with ABS and will degrade the part.

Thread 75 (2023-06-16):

Stronger ears for belt

locki-cz, 2023-06-16:
Please make ears little bit stronger, i breke it third time :(

Easy to edit, at least in F360
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

locki-cz, 2023-06-16:
[VORON_Tap_R8 stronger ears for belt.zip](https://github.com/VoronDesign/Voron-Tap/files/11775892/VORON_Tap_R8.stronger.ears.for.belt.zip)

In zip step and stl, please check.

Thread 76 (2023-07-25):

Placement of D1 LED on OptoTap v2.4

jonesuki, 2023-07-25:
I ordered OptoTap with the provided files (under OptoTap/Tap_Photosensor_PCB_v2/jlcpcb). The D1 LED are all placed upside down.

I contacted jlcpcb and they replied:
"Thanks for reaching out and sorry if any trouble caused.
Please kindly check the production file of this order in the attachment. For each order, we will make the production file and show it in Order history in a few hours after customers place the order. Customers can check it and if any problems, you can contact us in time.
For this order, the placement on the board is the same as the production file. We also notice that in the silkscreen layer, there is an arrow pointing to the board edge, and our engineering team make the placement according to the silkscreen. If the placement is incorrect, would you consider modify the arrow orienation on the silkscreen layer for your next orders? Silkscreen is very important for engineers and workers, so we sincerely suggest customers to make it better.
For these boards, if the placement is indeed not as you wish, could you try some resoldering on your side? Sincerely hope it will not cause you too much trouble."

I think they mean the white arrow on the silk screen is pointing downwards (to the board edge) and so should the arrow on D1 LED. This interpretation is just the opposite to the Voron team "...a little arrow that matches up with a corresponding arrow on the part".

Which one is the correct one or widely-accepted way of matching the component to the silk screen?
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

jonesuki, 2023-07-25:
P.S. The PCB still works after I enable dark mode. But there is no way to test it before connecting it to MCU.

jonesuki, 2023-07-26:
Further reply from JLCPCB:
"We can notice that the arrow is placed at the side far from the board edge. But it points to the side close to the board edge.
If you would like that the green arrow on D1 points towards the board center insteand of the board edge, you can put the arrow there, but it should be rotated 180 degree and points to the board center. "

This confirms JLCPCB interprets the arrow on D1 is placed so that its arrow pointing to the same direction as the white arrow on silk screen.

Is it feasible to change the silk screen to match the JLCPCB's interpretation?

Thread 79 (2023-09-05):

Magnet Holder possible improvement

xanxaz, 2023-09-05:
The Magnet holder screw position on the left side(front view), when you tighten it it will pull back the magnet holder and away from the set position(inward), making it a pain to set properly, maybe instead of a side screw, screw the part from the bottom? so it doesnt change the position/rotate the holder when tighten? the other side gets forced into the screw (outward) so it doesnt matter much.

igiannakas, 2024-04-05:
I agree with this - screwing the magnet from the side results in it twisting as the screw rotates. It makes it nearly impossible to retain the same position if you apply any meaningful torque to the screw. This would be a big QOL improvement.

Badnoob-327, 2024-06-27:
Sorry for such a late response, and thank you for your suggestion.
The magnet holding screws should not be overtightened, it will lead to problems cracking the thin print sections.  If our magnets are in contact properly, tighten the screw with moderate torque only.

Screwing from the bottom won't work without a reliable locknut method, the toolhead shakes too much, and the screws will back out over time.

Closed 2024-06-27.

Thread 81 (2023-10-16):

Inccorect stl file names in manual

wathiede, 2023-10-16:
The manual is still using r1 stl filenames, see this image 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

* All of them have the wrong suffix (r1 vs r8)
* `Tap_Magent_(Left|Right)_r1.stl` are now called `Tap_Center_(left|right)_r8.stl`
* `[a]Tap_Center_r1.stl` is now `[a]_Tap_Center_r8.stl` (extra _ before `Tap`)

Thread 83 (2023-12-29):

TabbedOpticalPCB_Left R8

Levitron86, 2023-12-29:
Hey thx for the great upgrade to version R8. Love the new Beld Clamp. Had some problems with loosen Belt and then i saw your update, well done.

But one point i recommend too change or add.

For the Optical PCB STL the lower left gap is missing. I could provide the corrected file for the R8 Version.

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

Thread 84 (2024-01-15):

Clarify role of solder jumper in operation of Optotap v2.4.1

thclark, 2024-01-15:
In the **Operation at 5V** section of the OptoTap readme

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

Most v2.4.1 PCBs (I've seen 3 in person now from 3 different sources) have no trace (by which I think is meant *bridge*?), just three segregated pads.

There are guidea round the internet stating to make sure our jumpers are correct, too. So the statement is confusing for people running 24V, as it creates an ambiguity around whether the 24v-centre pads should be bridged or not.

Here's what I think is true:
- If running 24v, you shouldn't bridge the 24v-centre pad
- If running 24v, and you do bridge the 24v-centre pads, it will still work but you won't benefit from overcurrent protection
- If running 5v, you shouldn't bridge the 5v-centre pad *initially*
- If running 5v and you experience too great a voltage loss (*) for the trigger to work correctly then you should bridge the 5v-centre pad. This will remove the overcurrent protection but reduce the voltage loss in the circuitry.

**If my assumptions are correct can someone please confirm, and I'll happily make a PR to tweak this README for clarification.**

*I assume this is measured between the ground and the signal output pins, but what's a sensible range that this output voltage should be, when operating correctly?

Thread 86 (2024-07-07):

Front pockets for diagonal SHCS heads undersized?

SebKuzminsky, 2024-07-07:
I'm on page 25 of the manual, attaching `Tap_Upper_PCB_r8.stl` and `Tap_Front_r8.stl`.  I think the pockets for the M3x20 SHCS heads are slightly undersized.  The screws got super hard to screw in towards the end, and started deforming the Front plastic.  I stopped applying torque for fear of damaging the plastic parts.

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
In the pic above, the straight edge is resting on the head of the SHCS (near 105 mm on the ruler), after i screwed it in as far as i dared.

I've printed all the parts for my 2.4r2 and Tap on an enclosed Prusa Mk4, and this is the first issue with fit that i've run in to.  So i think the printed parts match the STLs, and I'm suspicious of this particular STL.

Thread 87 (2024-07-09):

pg 28 is overly smarmy, plz explain how the magnet holders are supposed to mount

wirehead, 2024-07-09:
On pg 28 for the current manual, it says "We could say that there is only one way they fit, but we don’t want to underestimate you."

That's nice... but how *are* they supposed to fit?  The manual should probably say "so that you can see the non-heatset side through the side" because you really need to zoom in on the image to see the heat-set on the image.  Right now it's just a vague insult to the builder's intelligence.

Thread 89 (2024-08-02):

Add Warning About Semi-Transparent Printed Parts

ampp33, 2024-08-02:
This may be semi-obvious, but we should add a warning to the README and manual about ensuring the printed parts aren't transparent or semi-transparent if you plan on using the optical based sensor, because if the printed part isn't able to fully block the sensor's light then TAP will be less accurate and in some cases unsuable.

I printed the TAP center part using a bright orange ABS filament and noticed that TAP would seldom trigger properly, trigger late, or not trigger at all.  Once I swapped that part to a darker opaque based print all my issues were resolved.

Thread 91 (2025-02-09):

50 mm M3 bolts in CAD for [a]_Tap_Center_r8?

Zephyrus67, 2025-02-09:
What are the M3 50 mm bolts that goes through from bottom to almost top in the [a]_Tap_Center_r8 CAD model for?

Stiffening maybe?

Zep

timmit99, 2025-02-09:
Exactly yes, it's a way to add strength to the part utilizing existing hardware.

Zephyrus67, 2025-02-09:
Thanks I will try using it in next print I am doing. I am doing a R9 currently (or Zep R1 if you like). The reason is to attempt to get some of the very thin walls that seems to break often made thicker by redesigning.

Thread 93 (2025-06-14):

Fun Fact Voids™ - do these still exist in R8?

johyphenel, 2025-06-14:
IMO the changes from https://github.com/VoronDesign/Voron-Tap/issues/10 do not make it any more clear what someone should do to print these correctly.

1. It would be great to have screenshots from a slicer (doesn't matter which) of what the voids should look like when sliced correctly.
2. https://github.com/VoronDesign/Voron-Tap/issues/10 references tweaking "gap closing radius" or similar in slicers to make these voids show — the manual should include this along with a suggested value.
3. It's not clear to me that this advice actually works..? (see below)

The manual shows the `Tap_Front` part when giving the fun fact — so I'm trying with `Tap_Front_r8.stl`. In Orca slicer, setting `Slice gap closing radius` to `0.0`, `0.02`, or `0.049` (my profile default) seems to make no difference (and I don't think I see the voids?).

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

Using Ellis' preferred version of SuperSlicer & his current configs on github gives similar results:

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

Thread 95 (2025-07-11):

Attachment method (hex nut or heat-set) not specified for belt covers

paynterf, 2025-07-11:
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

The method for securing the M3x8 BHCS screws to the Tap_center part is not shown (there is a translucent drawing, but is that a hex nut or heat-set part).  The hole in the back of the Tap_center part appears to be sized for a heat-set screw, but there's not much plastic thickness.

kiwidave72, 2025-07-11:
It's a hex nut

paynterf, 2025-07-11:
Hmm, the actual piece doesn't have a hex-nut outline, so I'm not sure how it stays in place while the part is being attached to the rail carrier.  As I mentioned above, I wound up using two heat-set inserts, and they work - sort of.  I would print a new part and try again, but unfortunately my printer is down for Voron Tap installation ;)

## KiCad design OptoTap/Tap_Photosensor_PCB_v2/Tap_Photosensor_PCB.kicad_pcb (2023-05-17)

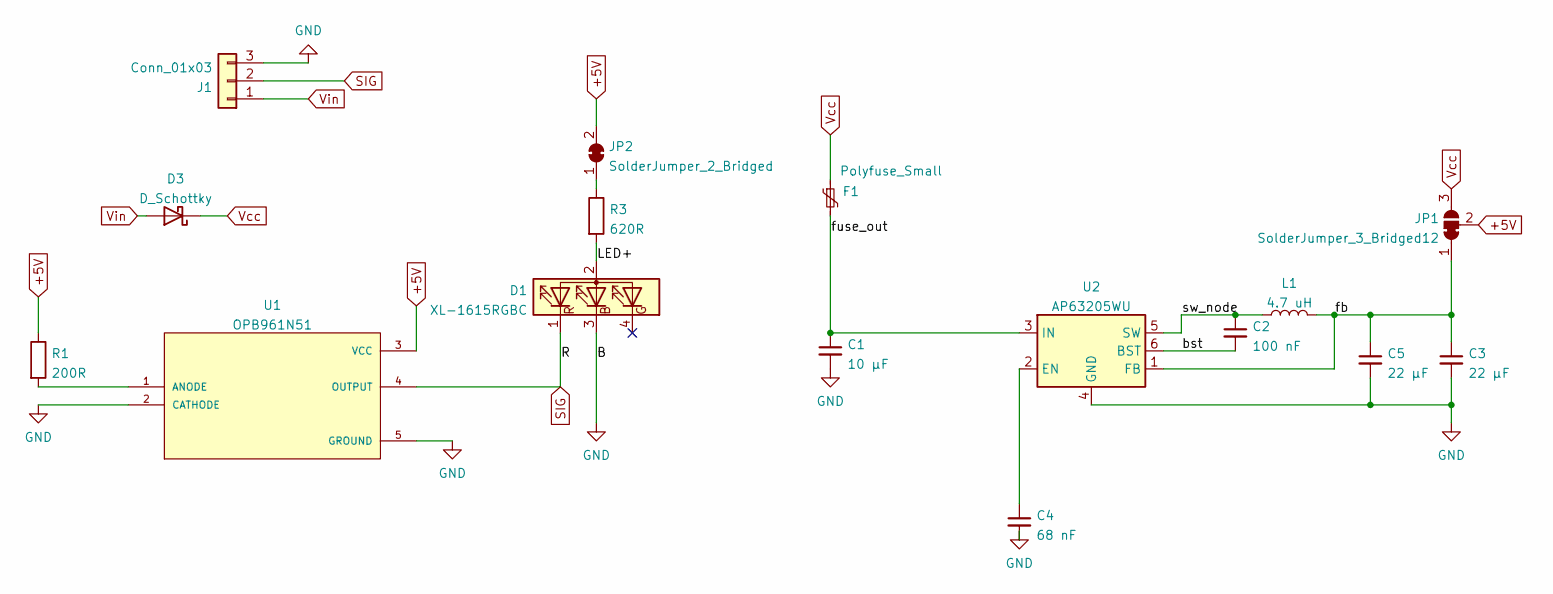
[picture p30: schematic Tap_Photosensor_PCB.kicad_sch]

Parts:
C1: 10 µF; C_0805_2012Metric; PARTNUM GRM21BR61H106KE43L; LCSC C440198
C2: 100 nF; C_0402_1005Metric; PARTNUM CL05B104KB54PNC; LCSC C307331
C3, C5: 22 µF; C_0603_1608Metric; PARTNUM GRM188R61A226ME15D; LCSC C84419
C4: 68 nF; C_0402_1005Metric; PARTNUM CC0402KRX7R9BB683; LCSC C354977
D1: XL-1615RGBC; LED_0606_1432; LCSC C965840
D3: D_Schottky; D_SOD-323; PARTNUM CUS10S30,H3F; LCSC C146335
F1: Polyfuse_Small; R_0805_2012Metric; PARTNUM SMD0805-010-33V; LCSC C2840557
J1: Conn_01x03; JST_PH_S3B-PH-K_1x03_P2.00mm_Horizontal
JP1: SolderJumper_3_Bridged12; SolderJumper-3_P1.3mm_Bridged12_RoundedPad1.0x1.5mm_NumberL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
JP2: SolderJumper_2_Bridged; SolderJumper-2_DARKMODE
L1: 4.7 uH; CKCS3010; PARTNUM CKCS3012-4.7uH/M; LCSC C354557
R1: 200R; R_0603_1608Metric; PARTNUM 0603WAF2000T5E; LCSC C8218
R3: 620R; R_0603_1608Metric; PARTNUM 0603WAF6200T5E; LCSC C23220
U1: OPB961N51; OPTO_EE-SX398_OPB666N; PARTREV D
U2: AP63205WU; TSOT-26; PARTNUM AP63205WU; LCSC C2071056

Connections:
+5V: JP1.2 (C), JP2.2 (B), R1.1, U1.3 (VCC)
/LED+: D1.2 (A), R3.2
/bst: C2.2, U2.6 (BST)
/fb: C3.1, C5.1, JP1.1 (A), L1.2, U2.1 (FB)
/fuse_out: C1.1, F1.2, U2.3 (IN)
/sw_node: C2.1, L1.1, U2.5 (SW)
GND: C1.2, C3.2, C4.2, C5.2, D1.3 (B), J1.3, U1.2 (CATHODE), U1.5 (GROUND), U2.4 (GND)
unnamed: JP2.1 (A), R3.1
unnamed: R1.2, U1.1 (ANODE)
unnamed: C4.1, U2.2 (EN)
SIG: D1.1 (R), J1.2, U1.4 (OUTPUT)
Vcc: D3.1 (K), F1.1, JP1.3 (B)
Vin: D3.2 (A), J1.1

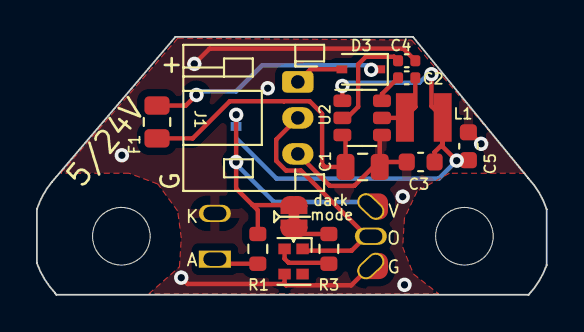
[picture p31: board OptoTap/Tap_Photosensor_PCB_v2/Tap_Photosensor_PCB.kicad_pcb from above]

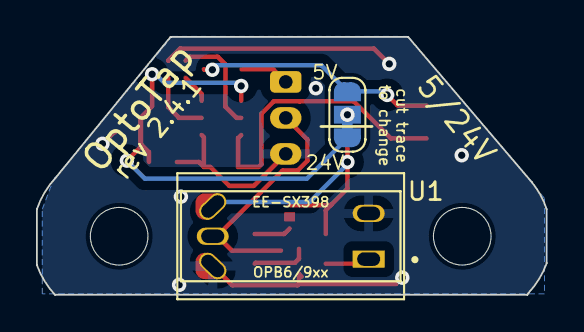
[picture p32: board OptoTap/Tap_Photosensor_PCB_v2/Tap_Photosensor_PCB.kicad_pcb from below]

Board: 2 copper layers, 28.3 x 14.3 mm, 16 parts (2 on the bottom side), 13 nets.

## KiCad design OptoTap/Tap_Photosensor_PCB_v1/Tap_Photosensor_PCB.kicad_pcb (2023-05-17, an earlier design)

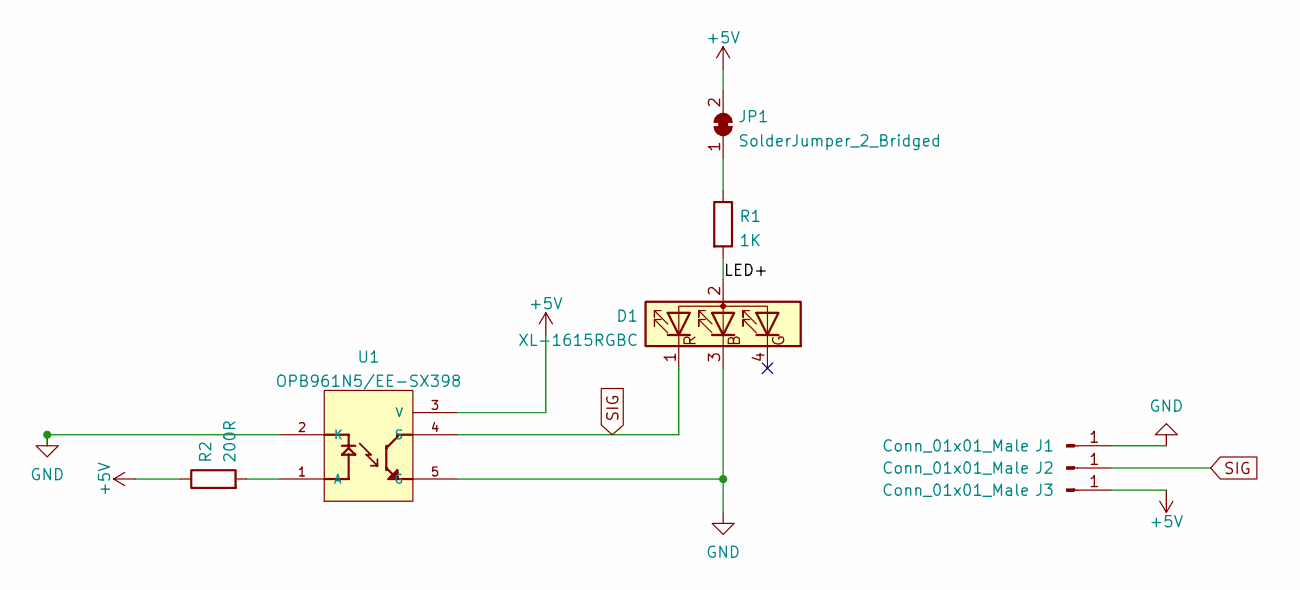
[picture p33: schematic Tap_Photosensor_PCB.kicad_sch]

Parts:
D1: XL-1615RGBC; LED_0606_1432; LCSC C965840
J1, J2, J3: Conn_01x01_Male; PinHeader_1x01_P2.54mm_Vertical
JP1: SolderJumper_2_Bridged; SolderJumper-2_P1.3mm_Bridged_RoundedPad1.0x1.5mm
R1: 1K; R_0805_2012Metric; LCSC C17513
R2: 200R; R_0805_2012Metric; LCSC C17540
U1: OPB961N5/EE-SX398; OPTO_EE-SX398_OPB666N; PARTREV NA

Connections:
+5V: J3.1, JP1.2 (B), R2.1, U1.3 (V)
/LED+: D1.2 (A), R1.2
GND: D1.3 (B), J1.1, U1.2 (K), U1.5 (G)
unnamed: JP1.1 (A), R1.1
unnamed: R2.2, U1.1 (A)
SIG: D1.1 (R), J2.1, U1.4 (S)

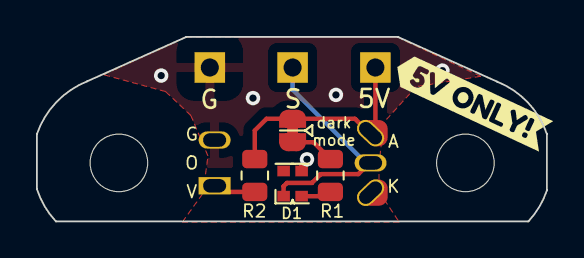
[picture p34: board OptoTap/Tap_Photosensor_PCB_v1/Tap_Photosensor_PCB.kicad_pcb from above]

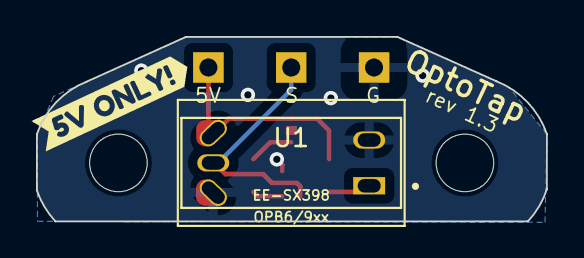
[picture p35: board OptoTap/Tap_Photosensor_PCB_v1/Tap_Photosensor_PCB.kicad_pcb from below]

Board: 2 copper layers, 28.3 x 10.2 mm, 10 parts (2 on the bottom side), 6 nets.

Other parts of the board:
kibuzzard-6366BF75: G***; kibuzzard-6366BF75
kibuzzard-6366C103: G***; kibuzzard-6366C103

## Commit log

2022-11-23 Add bom (#1)
    * Create TAP_BOM
    * Delete TAP_BOM
    * Create TAP_BOM.txt
    * Delete TAP_BOM.txt
    * Create TAP_BOM.md
    * Update TAP_BOM.md
    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
2022-11-27 Initial commit of the STLs and CAD for Voron-Tap (#2)
    * Create Readme.md
    * readme.md
    * Create readme.md
    * initial commit of stls
    * CAD upload
    * Delete readme.md
    No need for a readme here
    * Delete readme.md
    no need for a readme here
    * Creating OptoTap space
    * adding tap_klipper_instructions.md
    * Delete tap_klipper_instructions.md
    added wrong file...
    * readding tap_klipper_instructions
    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
    [Tap_Front_r1.stl, Tap_Magnet_Left_r1.stl, Tap_Magnet_Right_r1.stl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]
2022-11-27 Optotap (#4)
    * removed zip archive
    * added optotap files
    [Tap_Photosensor_PCB-CuBottom.gbr, Tap_Photosensor_PCB-CuTop.gbr, Tap_Photosensor_PCB-EdgeCuts.gbr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]
2022-11-27 Add missing tool STLs (#5)
    [MGN9_Assembly_Tool.stl, Printed_Cut_Guide.stl]
2022-11-27 fixed PCB assembly files (#9)
    [BOM-Tap_Photosensor_PCB.csv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]
2022-11-27 updated kicad files with proper resistor values (#11)
    [BOM-Tap_Photosensor_PCB.csv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]
2022-11-28 fixed merge conflict (#12)
    [BOM-Tap_Photosensor_PCB.csv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]
2022-11-28 fixing images in manual, also minor text truncations (#16)
    * temp to hold directory open
    * removing old
    * updated optotap link
    * removing temp file
    * Create temp
    * Delete Assembly_Manual_Tap.pdf
    * Add files via upload
    fixed issues with pixelated drawings and truncated texts
    * Delete temp
    * fixing a few more issues noticed
2022-11-29 Reducing chamfer on Tap_center per issue #15 (#17)
    * Addressing #15
    https://github.com/VoronDesign/Voron-Tap/issues/15 I reduced the chamfer. while in there I also update the part to voron-red
    * reduced chamfer for more mgn12 clearance
    * Delete [a]Tap_Center_r1.stl
    removing older version with too much chamfer https://github.com/VoronDesign/Voron-Tap/issues/15
    * updating cad for issue 15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
    [[a]Tap_Center_r1.stl, [a]Tap_Center_r2.stl]
2022-11-29 fixed missing support in [a]Tap_Center_r2 (#18)
    * putting back the support which went missing in r2
    * Delete [a]Tap_Center_r2.stl
    removing the support-less version
    * Create changelog.md
    Adding a changelog for summarizing part changes
    * correcting part names, adding link
    * re-added missing center support from r2
    * Delete VORON_Tap_r2.step
    removing older cad
    * Update changelog.md
    [[a]Tap_Center_r2.stl, [a]Tap_Center_r3.stl]
2022-12-17 Mid december update (#32)
    * Mid-December tap update
    Added D2HW variant
    minor adjustments to wired and PCB optical sensor position
    minor clearance adj to m3x12 endstop
    clearance for solder blobs
    * remove prev cad version
    * tightened up optical channel by .6mm
    * mid december update
    D2HW variant introduced
    minor changes to optical sensor positions to improve precision
    added reinforcement to center above magnet holders
    * removing older version
    * Delete Tap_Upper_PCB_r1.stl
    removing older version
    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
    [Tap_Front_r1.stl, Tap_Front_r2.stl, Tap_Upper_D2HW_r1.stl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]
2022-12-17 Update tap_klipper_instructions.md (#33)
    - closes issue #27
    - adds reminder to remove old autosaved `position_endstop` value for `stepper_z` if present
    - improves readability
2023-01-02 Add "Z" ("w/ wires") to the PN (OPB991L11Z). (#39)
2023-01-03 Fix for X-Axis binding (#43)
    * Delete Tap_Upper_Wired_r1.stl
    * Delete [a]Tap_Center_r3.stl
    Mid december update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
    [[a]Tap_Center_r4.stl, [a]Tap_Center_r5.stl]
2023-01-04 Update to the jan 3 update (#44)
    fixing a minor ledge artifact in tap_center.
    * fixed a minor ledge artifact
    * Delete 1_3_23updatelog.png
    updating
    updated to include 2 more changes
    * Delete 1_3_23updatelog.png
    * Delete 1_3_23updatelog.png
    * Delete [a]Tap_Center_r5.stl
    * Delete VORON_Tap_r4.step
    * Delete VORON_Tap_r5.step
    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
    [[a]Tap_Center_r5.stl, [a]Tap_Center_r6.stl]
2023-01-14 update magnet holders from CAD (#46)
    [Tap_Magnet_Left_r1.stl, Tap_Magnet_Left_r2.stl, Tap_Magnet_Right_r1.stl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]
2023-03-03 updated OptoTap boards (#53)
    * updated OptoTap boards
    * changed footprint text to specify EE-SX398
    * added solder jig step
    * fixed link
    [BOM-Tap_Photosensor_PCB.csv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]
2023-05-01 Updating to RC8 (#62)
    * Updating to RC8
    badnoob: rename step to VORON_Tap_RC8
    badnoob: r8 stl files uploaded
    badnoob: add R8 readme
    jade: move rc8 images, update readme image paths
    * Standardize file names, remove old revisions
    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
    [Tap_Belt_Cover_r8_x2.stl, Tap_Center_left_r8.stl, Tap_Center_r8.stl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]
2023-05-06 Updated BOM.md to RC8 (#64)
2023-05-08 Renamed "Tap_Center_r8.stl" to "[a]_Tap_Center_r8.stl" and "Tap_Belt_Cover_r8_x2.stl" to "[a]_Tap_Belt_Cover_r8_x2.stl" (#66)
    * Renamed to denote accent part
    Keeping in line with prior releases and standard Voron printed part naming conventions, I've renamed "Tap_Center_r8.stl" to "[a]_Tap_Center_r8.stl"
    * Renamed "Tap_Belt_Cover_r8_x2.stl" to "[a]_Tap_Belt_Cover_r8_x2.stl"
    Keeping in line with Voron printed part naming conventions, "Tap_Belt_Cover_r8_x2.stl" has been renamed to "[a]_Tap_Belt_Cover_r8_x2.stl"
    [[a]_Tap_Belt_Cover_r8_x2.stl, [a]_Tap_Center_r8.stl]
2023-05-17 Opto24 (#68)
    * updated inductor info
    * updated STEP and kicad
    * updated README with LED ordering info
    * fixed bad save
    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
    [Tap_Photosensor_PCB.STEP, Tap_Photosensor_PCB.kicad_pcb, Tap_Photosensor_PCB.kicad_sch]
2023-06-14 doc: add nr of pins for JST-PH connector (#69)
2023-08-18 clarified info on 5v operation (#77)
